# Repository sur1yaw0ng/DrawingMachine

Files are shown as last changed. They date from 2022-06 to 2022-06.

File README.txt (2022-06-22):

# DrawingMachine

###	FABRICATION NOTES	###
The structural parts we ordered didn't have the same cross section as the pieces that
came on the Ender. Reference drawings are included in the rhino model, but the original
ender pieces have a 45 degree chamfer to accept the geometry of the wheel more readily.
I didn't understand at first how the adjustment on the wheels worked, so assumed that the
best way to get the wheels to work with the new pieces was to machine a chamfer in the relevant tracks.
The chamfer was done on the bridgeport with a 45 degree router bit. Even though it's not strictly
necessary, I think that having some amount of chamfer will help the wheels operate as they should, 
and stay firmly seated in the track.

The 3d Printed parts included in the model are the first iteration I printed, but the tolerance was too
tight for the parts that are supposed to fit into the t-slots, and the pieces failed. Soon to re-tool the parts
for a second round.

The bed modeled is configured to have four support/adjustment points as on the original ender, may be
worth adding more since the bed is so large, to help avoid flexing?

###	CODE NOTES		###
All the code necessary is in the foilder Marlin-bugfix-1.1.x, which is the version compatible with the 8-bit
board present in the prototype. After the bootloader is burned with the arduino, the arduino IDE should be able
load new firmware onto the ender via a direct USB connection. Newer motherboards will be compatible with newer 
versions of Marlin, as well as accept new firmware via the SD card

###	RHINO NOTES	###
Use command SaveSmall to make files smaller than 100mb to work with GitHub

###	FLASHING BOOTLOADER	###
Only necessary for older motherboards. Requires Arduino Uno/Micro and jumper wires. Tutorials linked below:
https://howchoo.com/ender3/ender-3-bootloader-firmware-update-marlin
https://all3dp.com/2/ender-3-pro-firmware-update-marlin/
https://www.th3dstudio.com/hc/guides/bootloader/bootloader-flashing-guide-cr-10-ender-2-3-5-wanhao-i3-anet-1284p-boards/

###	SPLASH SCREEN		###
Black and white image at 128 x 64 pixels, input into link provided below
to convert into text bitmap to input in code.
Copy and paste resulting text into _Bootscreen.h using Arduino IDE

https://marlinfw.org/tools/u8glib/converter.html

###	BED SIZE		###
Bed size is defined in Configuration.h, lines 877-878

###	MACHINE NAME		###
Machine name is defined in Configuration.h, line 132

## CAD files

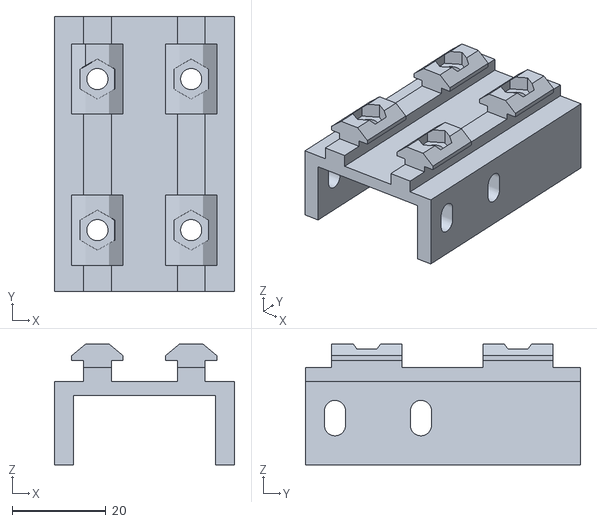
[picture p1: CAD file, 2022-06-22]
drawingMachinePrintedPartsSTLs/pulleyMount.stl
38.4 x 58.7 x 25.8

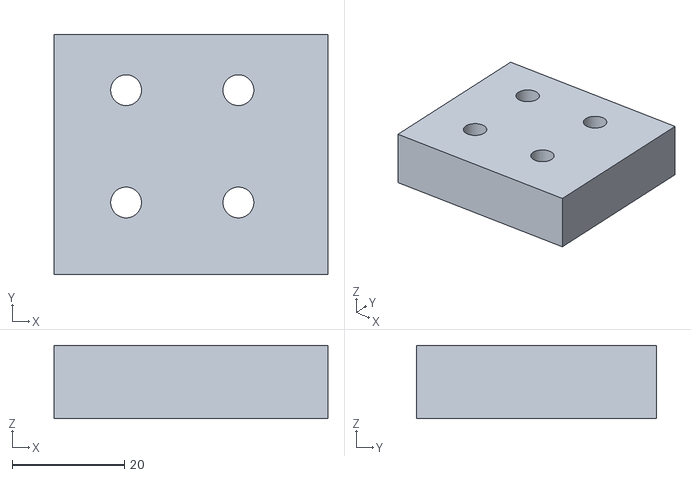
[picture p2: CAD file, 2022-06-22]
drawingMachinePrintedPartsSTLs/spacer.stl
48.8 x 42.8 x 13.1

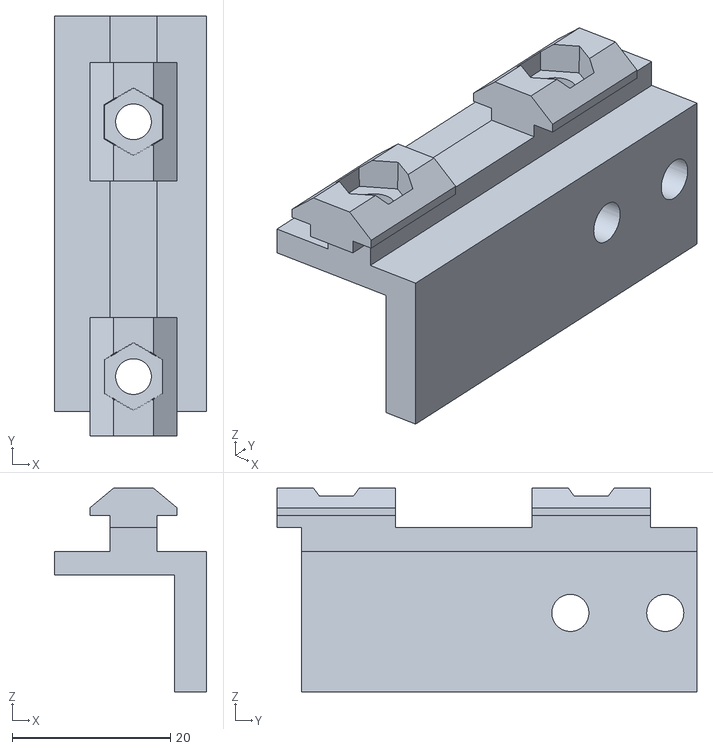
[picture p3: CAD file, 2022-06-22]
drawingMachinePrintedPartsSTLs/yStopMount.stl
19.2 x 53.1 x 25.8

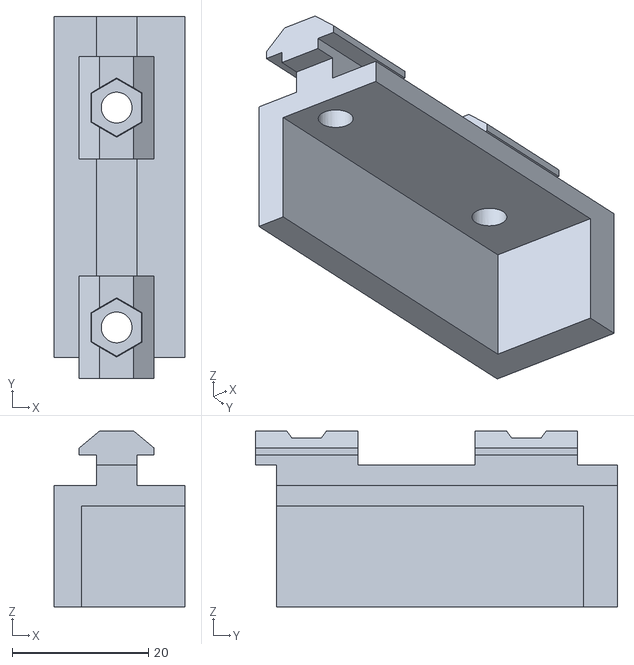
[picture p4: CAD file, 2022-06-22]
drawingMachinePrintedPartsSTLs/motorMount.stl
19.2 x 53.1 x 25.8

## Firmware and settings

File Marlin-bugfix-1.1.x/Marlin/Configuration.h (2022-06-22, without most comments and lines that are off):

#define CONFIGURATION_H
#define CONFIGURATION_H_VERSION 010109
#define STRING_CONFIG_H_AUTHOR "(thisiskeithb, Ender-3)" // Who made the changes.
#define SHOW_BOOTSCREEN
#define STRING_SPLASH_LINE1 SHORT_BUILD_VERSION // will be shown during bootup in line 1
#define STRING_SPLASH_LINE2 WEBSITE_URL         // will be shown during bootup in line 2
#define SHOW_CUSTOM_BOOTSCREEN
#define CUSTOM_STATUS_SCREEN_IMAGE
#define SERIAL_PORT 0
#define BAUDRATE 115200
  #define MOTHERBOARD BOARD_MELZI_CREALITY
#define CUSTOM_MACHINE_NAME "DrawingMachinePrototype"
#define EXTRUDERS 1
#define DEFAULT_NOMINAL_FILAMENT_DIA 1.75
#define POWER_SUPPLY 0
#define TEMP_SENSOR_0 1
#define TEMP_SENSOR_1 0
#define TEMP_SENSOR_2 0
#define TEMP_SENSOR_3 0
#define TEMP_SENSOR_4 0
#define TEMP_SENSOR_BED 0
#define TEMP_SENSOR_CHAMBER 0
#define DUMMY_THERMISTOR_998_VALUE 25
#define DUMMY_THERMISTOR_999_VALUE 100
#define MAX_REDUNDANT_TEMP_SENSOR_DIFF 10
#define TEMP_RESIDENCY_TIME 10  // (seconds)
#define TEMP_HYSTERESIS 3       // (degC) range of +/- temperatures considered "close" to the target one
#define TEMP_WINDOW     1       // (degC) Window around target to start the residency timer x degC early.
#define TEMP_BED_RESIDENCY_TIME 10  // (seconds)
#define TEMP_BED_HYSTERESIS 3       // (degC) range of +/- temperatures considered "close" to the target one
#define TEMP_BED_WINDOW     1       // (degC) Window around target to start the residency timer x degC early.
#define HEATER_0_MINTEMP 5
#define HEATER_1_MINTEMP 5
#define HEATER_2_MINTEMP 5
#define HEATER_3_MINTEMP 5
#define HEATER_4_MINTEMP 5
#define BED_MINTEMP 5
#define HEATER_0_MAXTEMP 275
#define HEATER_1_MAXTEMP 275
#define HEATER_2_MAXTEMP 275
#define HEATER_3_MAXTEMP 275
#define HEATER_4_MAXTEMP 275
#define BED_MAXTEMP 125
#define PIDTEMP
#define BANG_MAX 255     // Limits current to nozzle while in bang-bang mode; 255=full current
#define PID_MAX BANG_MAX // Limits current to nozzle while PID is active (see PID_FUNCTIONAL_RANGE below); 255=full current
#define PID_K1 0.95      // Smoothing factor within any PID loop
  #define PID_AUTOTUNE_MENU // Add PID Autotune to the LCD "Temperature" menu to run M303 and apply the result.
  #define PID_FUNCTIONAL_RANGE 10 // If the temperature difference between the target temperature and the actual temperature
  #define DEFAULT_Kp 21.73
  #define DEFAULT_Ki 1.54
  #define DEFAULT_Kd 76.55
#define MAX_BED_POWER 255 // limits duty cycle to bed; 255=full current
#define PREVENT_COLD_EXTRUSION
#define EXTRUDE_MINTEMP 170
#define PREVENT_LENGTHY_EXTRUDE
#define EXTRUDE_MAXLENGTH 200
#define THERMAL_PROTECTION_HOTENDS // Enable thermal protection for all extruders
#define THERMAL_PROTECTION_BED     // Enable thermal protection for the heated bed
#define USE_XMIN_PLUG
#define USE_YMIN_PLUG
#define USE_ZMIN_PLUG
#define ENDSTOPPULLUPS
#define X_MIN_ENDSTOP_INVERTING false // set to true to invert the logic of the endstop.
#define Y_MIN_ENDSTOP_INVERTING false // set to true to invert the logic of the endstop.
#define Z_MIN_ENDSTOP_INVERTING false // set to true to invert the logic of the endstop.
#define X_MAX_ENDSTOP_INVERTING false // set to true to invert the logic of the endstop.
#define Y_MAX_ENDSTOP_INVERTING false // set to true to invert the logic of the endstop.
#define Z_MAX_ENDSTOP_INVERTING false // set to true to invert the logic of the endstop.
#define Z_MIN_PROBE_ENDSTOP_INVERTING false // set to true to invert the logic of the probe.
#define DEFAULT_AXIS_STEPS_PER_UNIT   { 80, 80, 400, 93 }
#define DEFAULT_MAX_FEEDRATE          { 500, 500, 5, 25 }
#define DEFAULT_MAX_ACCELERATION      { 500, 500, 100, 5000 }
#define DEFAULT_ACCELERATION          500    // X, Y, Z and E acceleration for printing moves
#define DEFAULT_RETRACT_ACCELERATION  500    // E acceleration for retracts
#define DEFAULT_TRAVEL_ACCELERATION   500    // X, Y, Z acceleration for travel (non printing) moves
#define DEFAULT_XJERK                 10.0
#define DEFAULT_YJERK                 10.0
#define DEFAULT_ZJERK                  0.3
#define DEFAULT_EJERK                  5.0
#define Z_MIN_PROBE_USES_Z_MIN_ENDSTOP_PIN
#define X_PROBE_OFFSET_FROM_EXTRUDER 10  // X offset: -left  +right  [of the nozzle]
#define Y_PROBE_OFFSET_FROM_EXTRUDER 10  // Y offset: -front +behind [the nozzle]
#define Z_PROBE_OFFSET_FROM_EXTRUDER 0   // Z offset: -below +above  [the nozzle]
#define MIN_PROBE_EDGE 10
#define XY_PROBE_SPEED 8000
#define Z_PROBE_SPEED_FAST HOMING_FEEDRATE_Z
#define Z_PROBE_SPEED_SLOW (Z_PROBE_SPEED_FAST / 2)
#define Z_CLEARANCE_DEPLOY_PROBE   10 // Z Clearance for Deploy/Stow
#define Z_CLEARANCE_BETWEEN_PROBES  5 // Z Clearance between probe points
#define Z_CLEARANCE_MULTI_PROBE     5 // Z Clearance between multiple probes
#define Z_PROBE_LOW_POINT          -2 // Farthest distance below the trigger-point to go before stopping
#define Z_PROBE_OFFSET_RANGE_MIN -20
#define Z_PROBE_OFFSET_RANGE_MAX 20
#define X_ENABLE_ON 0
#define Y_ENABLE_ON 0
#define Z_ENABLE_ON 0
#define E_ENABLE_ON 0 // For all extruders
#define DISABLE_X false
#define DISABLE_Y false
#define DISABLE_Z false
#define DISABLE_E false // For all extruders
#define DISABLE_INACTIVE_EXTRUDER false // Keep only the active extruder enabled.
#define INVERT_X_DIR true
#define INVERT_Y_DIR true
#define INVERT_Z_DIR false
#define INVERT_E0_DIR true
#define INVERT_E1_DIR false
#define INVERT_E2_DIR false
#define INVERT_E3_DIR false
#define INVERT_E4_DIR false
#define X_HOME_DIR -1
#define Y_HOME_DIR -1
#define Z_HOME_DIR -1
#define X_BED_SIZE 457
#define Y_BED_SIZE 381
#define X_MIN_POS 0
#define Y_MIN_POS 0
#define Z_MIN_POS 0
#define X_MAX_POS X_BED_SIZE
#define Y_MAX_POS Y_BED_SIZE
#define Z_MAX_POS 250
#define MIN_SOFTWARE_ENDSTOPS
  #define MIN_SOFTWARE_ENDSTOP_X
  #define MIN_SOFTWARE_ENDSTOP_Y
  #define MIN_SOFTWARE_ENDSTOP_Z
#define MAX_SOFTWARE_ENDSTOPS
  #define MAX_SOFTWARE_ENDSTOP_X
  #define MAX_SOFTWARE_ENDSTOP_Y
  #define MAX_SOFTWARE_ENDSTOP_Z
#define HOMING_FEEDRATE_XY (20*60)
#define HOMING_FEEDRATE_Z  (4*60)
#define EEPROM_SETTINGS // Enable for M500 and M501 commands
#define EEPROM_CHITCHAT   // Give feedback on EEPROM commands. Disable to save PROGMEM.
#define HOST_KEEPALIVE_FEATURE        // Disable this if your host doesn't like keepalive messages
#define DEFAULT_KEEPALIVE_INTERVAL 2  // Number of seconds between "busy" messages. Set with M113.
#define BUSY_WHILE_HEATING            // Some hosts require "busy" messages even during heating
#define PREHEAT_1_TEMP_HOTEND 185
#define PREHEAT_1_TEMP_BED     45
#define PREHEAT_1_FAN_SPEED   255 // Value from 0 to 255
#define PREHEAT_2_TEMP_HOTEND 240
#define PREHEAT_2_TEMP_BED      0
#define PREHEAT_2_FAN_SPEED   255 // Value from 0 to 255
#define PRINTJOB_TIMER_AUTOSTART
#define LCD_LANGUAGE en
#define DISPLAY_CHARSET_HD44780 WESTERN
#define SDSUPPORT
#define SPEAKER
#define CR10_STOCKDISPLAY
#define SOFT_PWM_SCALE 0
#define SERVO_DELAY { 300 }

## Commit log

2022-06-22 Initial commit
    Uploaded all the files, links, and documentation for the first prototype
    [Configuration.h, Configuration_adv.h]
2022-06-22 Version 1 3d Prints
    First version of 3d printed parts (STL) uploaded
    [motorMount.stl, pulleyMount.stl, spacer.stl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]

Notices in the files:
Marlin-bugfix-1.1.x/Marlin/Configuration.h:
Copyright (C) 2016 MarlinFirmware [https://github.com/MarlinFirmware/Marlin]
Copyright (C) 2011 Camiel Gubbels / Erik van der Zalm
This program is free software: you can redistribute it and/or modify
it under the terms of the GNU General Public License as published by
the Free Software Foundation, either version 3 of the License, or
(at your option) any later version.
